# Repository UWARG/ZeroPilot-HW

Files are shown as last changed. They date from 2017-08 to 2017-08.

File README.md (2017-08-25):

# ZeroPilot
WARG's future autopilot to replace the PicPilot

# Installation

After cloning the repo, run `git submodule update --init --recursive` to pull in all the submodules.

If you see rendering issues in the schematic or pcb, check to make sure you've got the most updated submodules. To do this, run: `git submodule update --recursive --remote`

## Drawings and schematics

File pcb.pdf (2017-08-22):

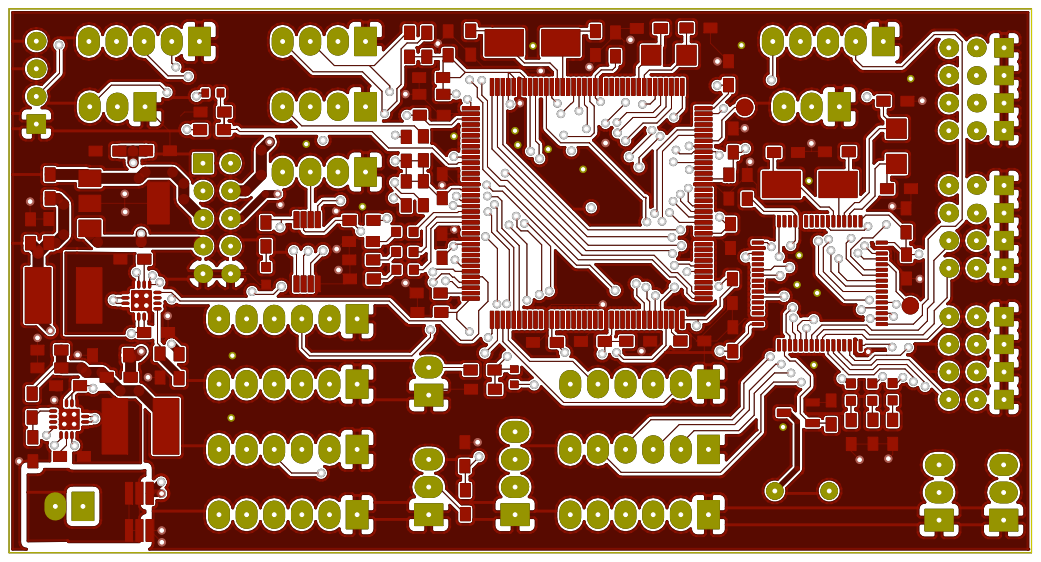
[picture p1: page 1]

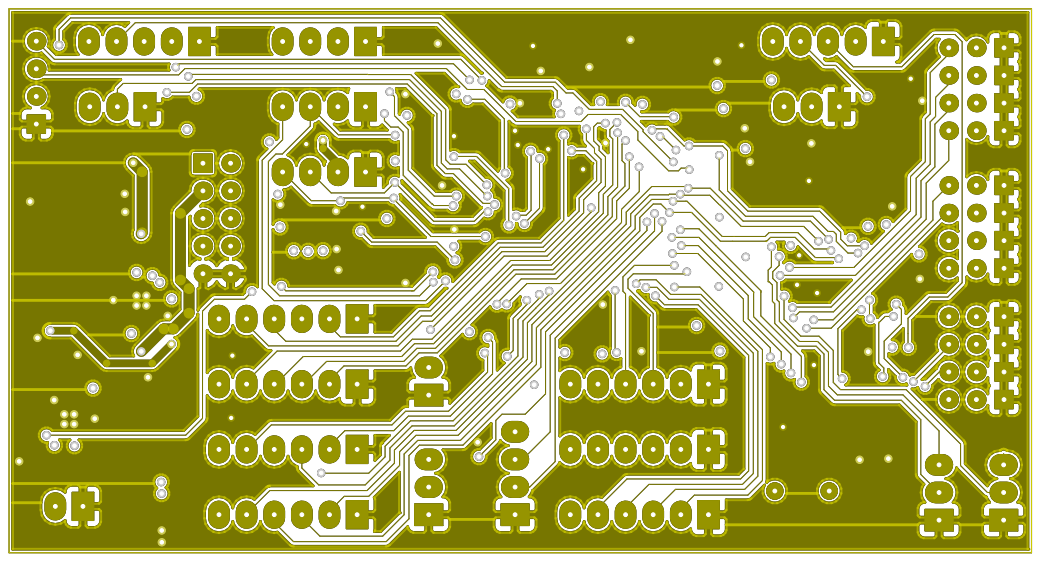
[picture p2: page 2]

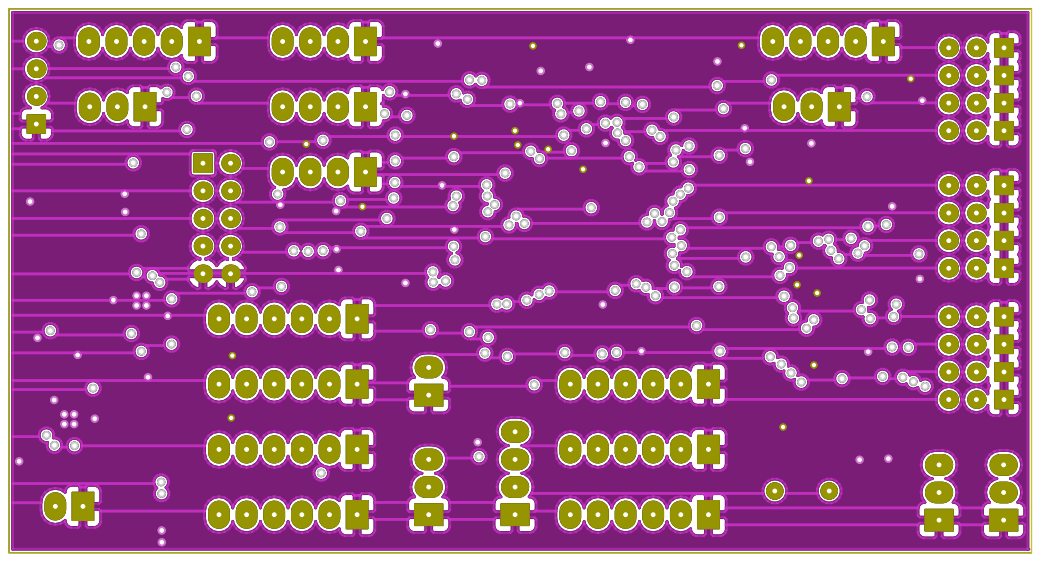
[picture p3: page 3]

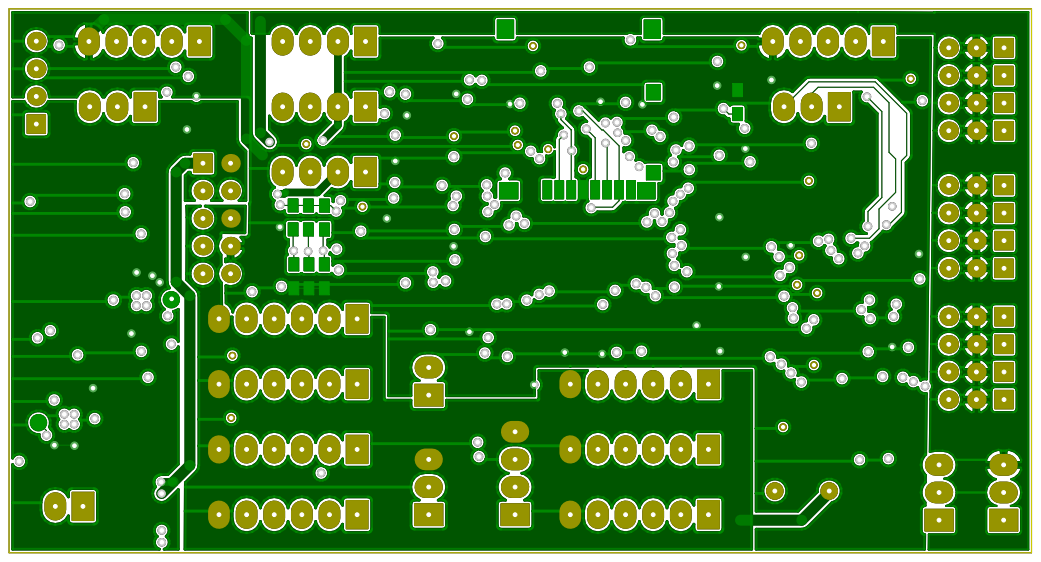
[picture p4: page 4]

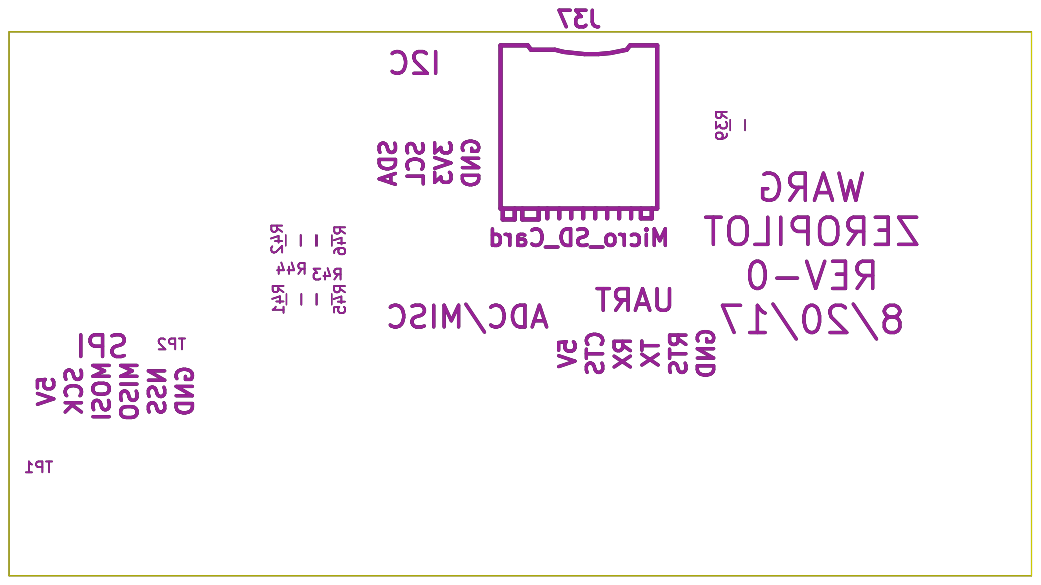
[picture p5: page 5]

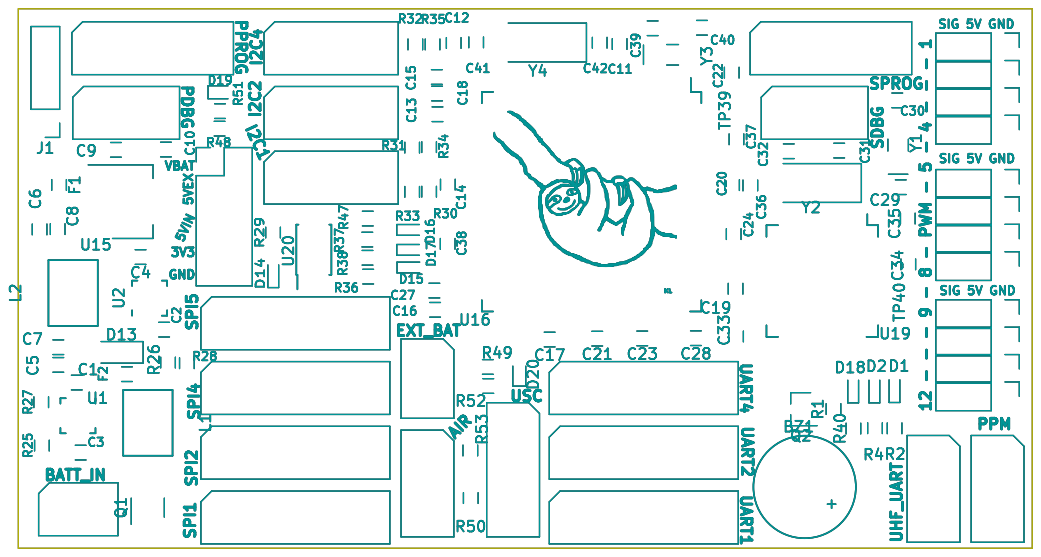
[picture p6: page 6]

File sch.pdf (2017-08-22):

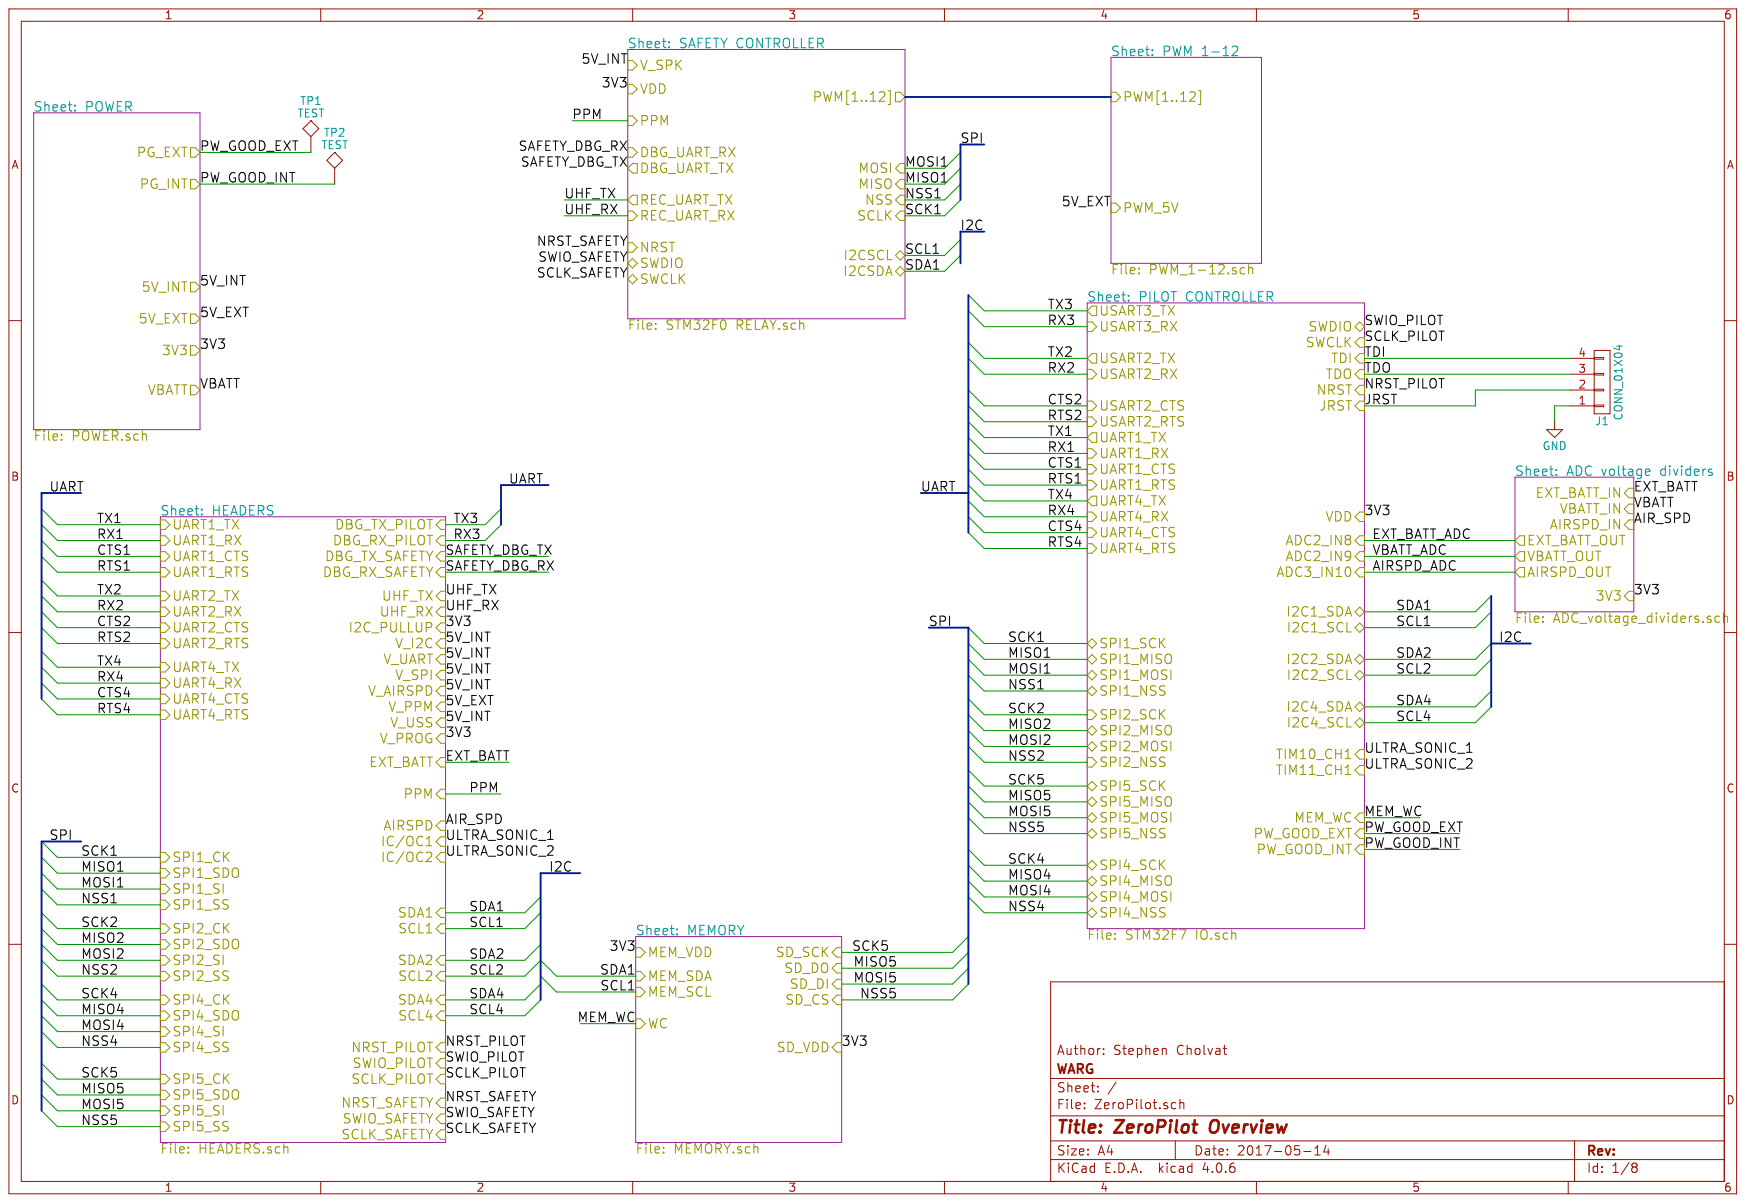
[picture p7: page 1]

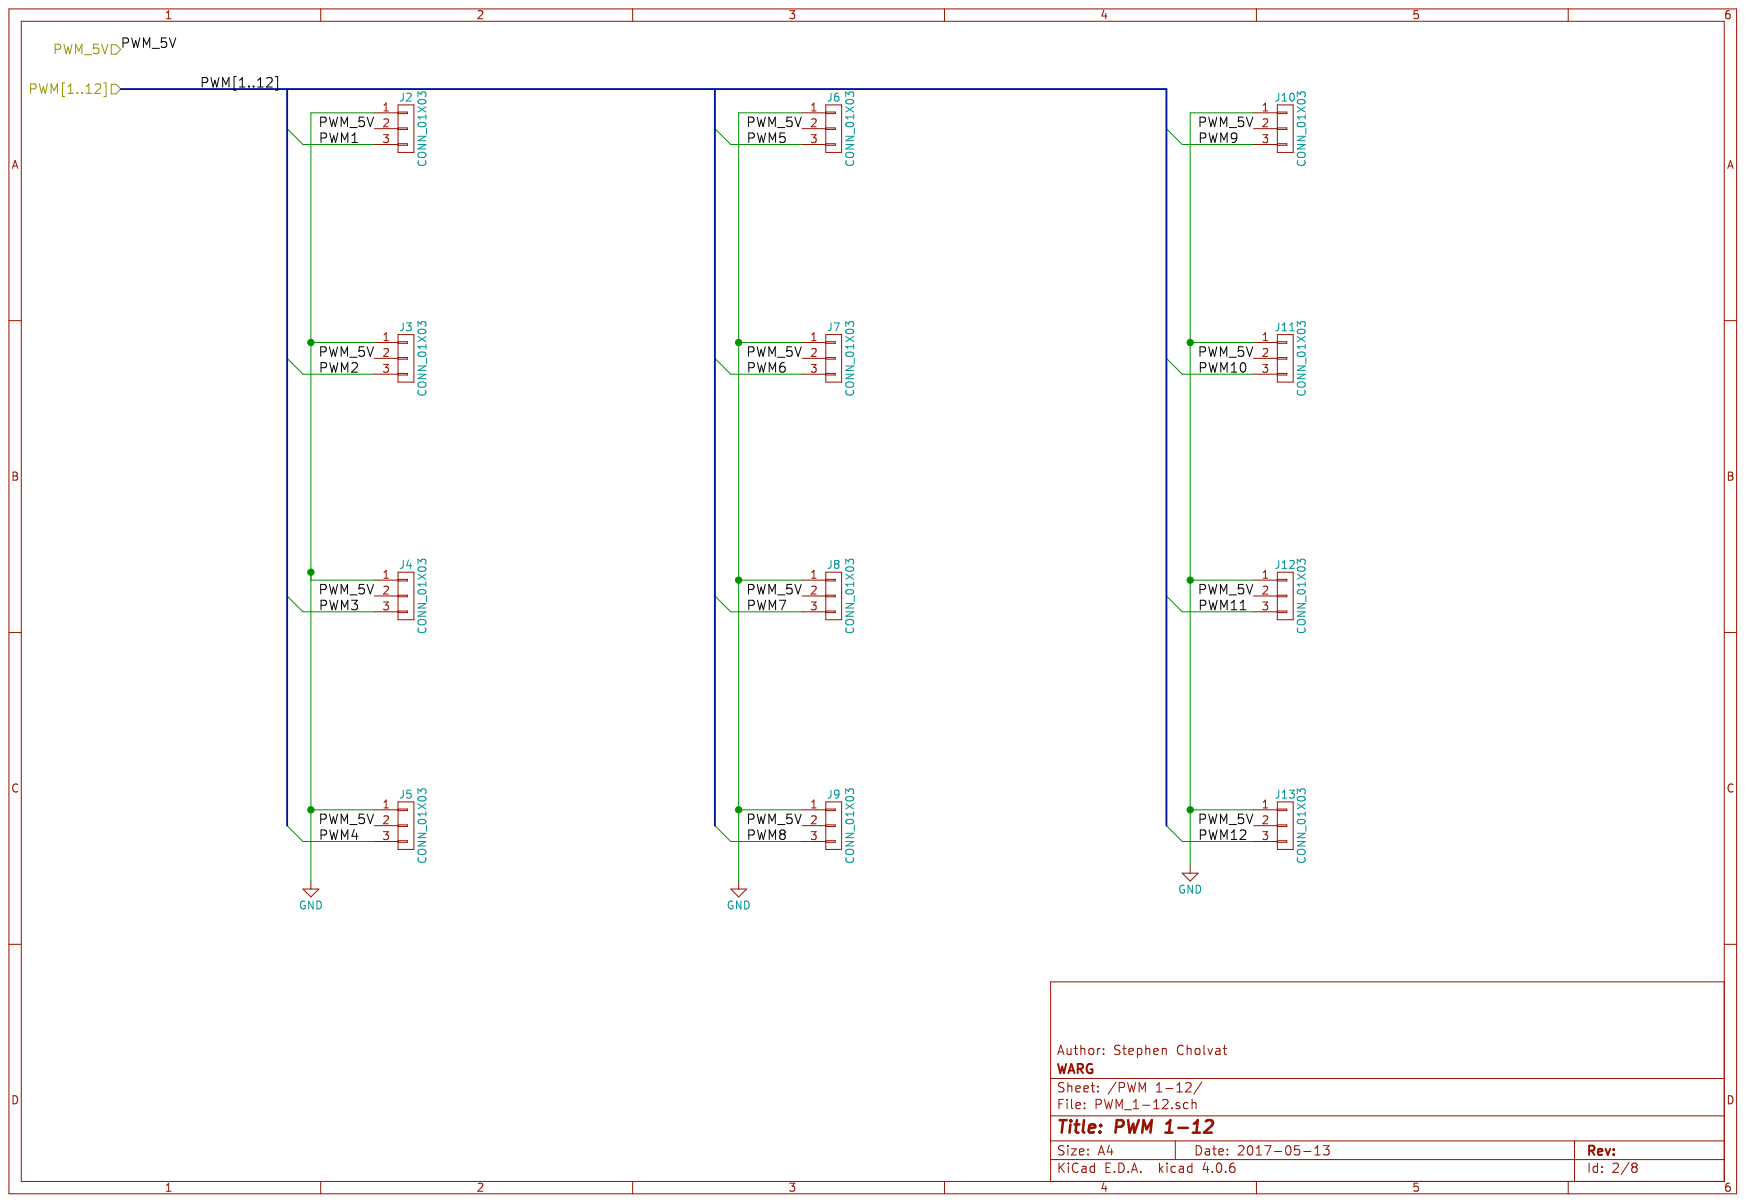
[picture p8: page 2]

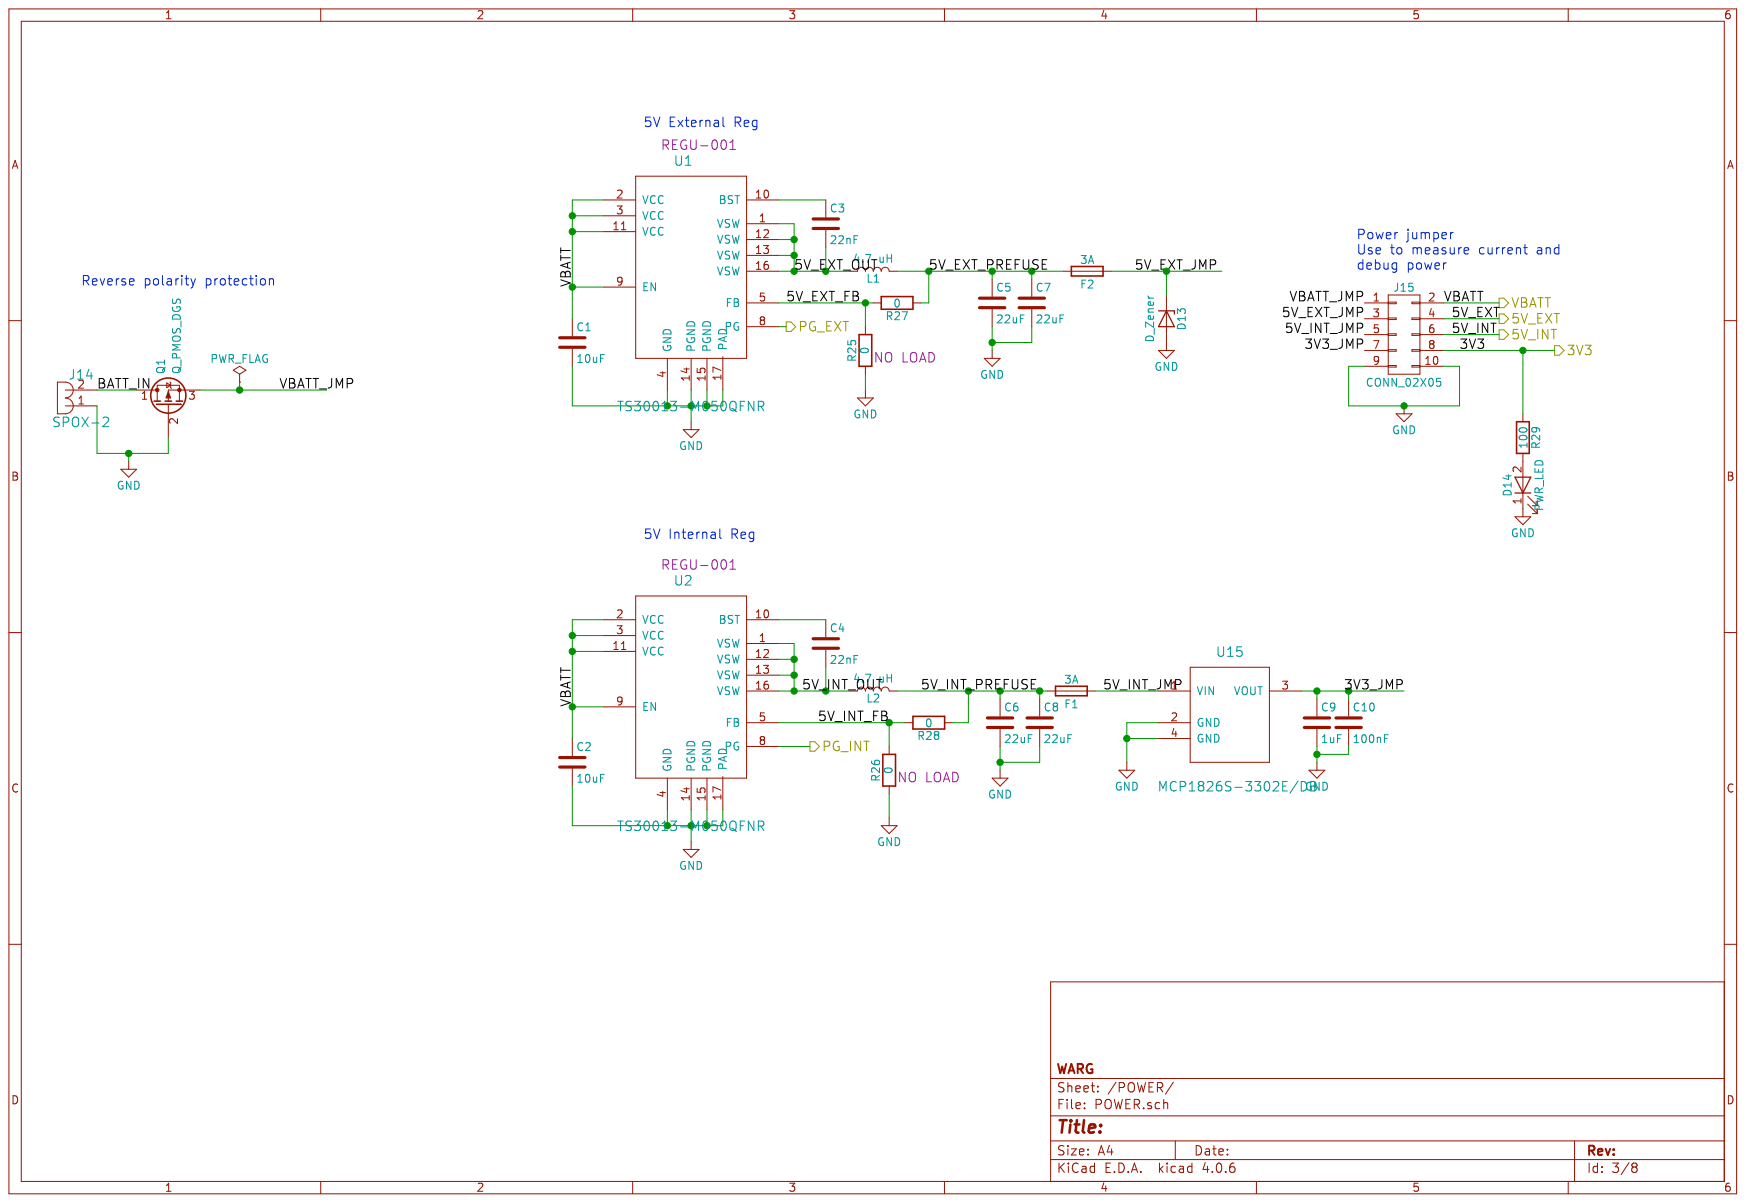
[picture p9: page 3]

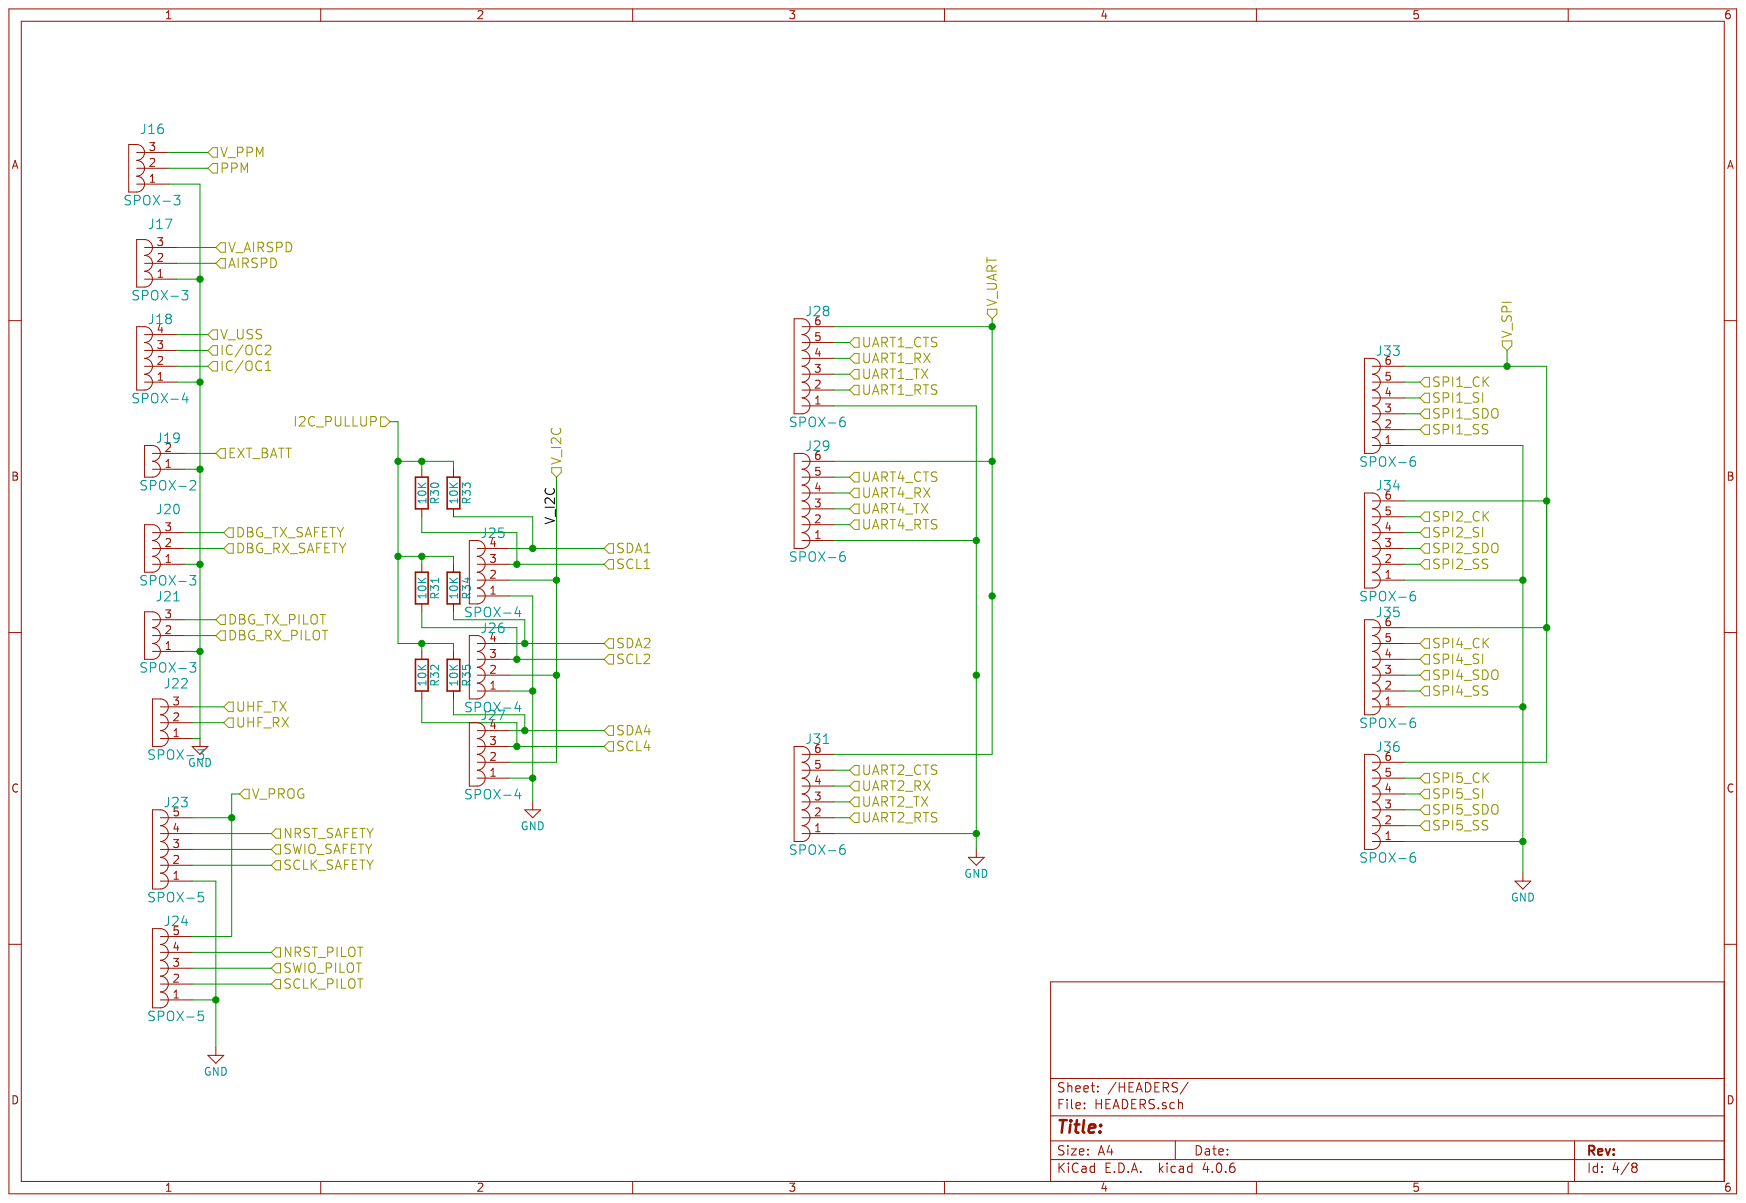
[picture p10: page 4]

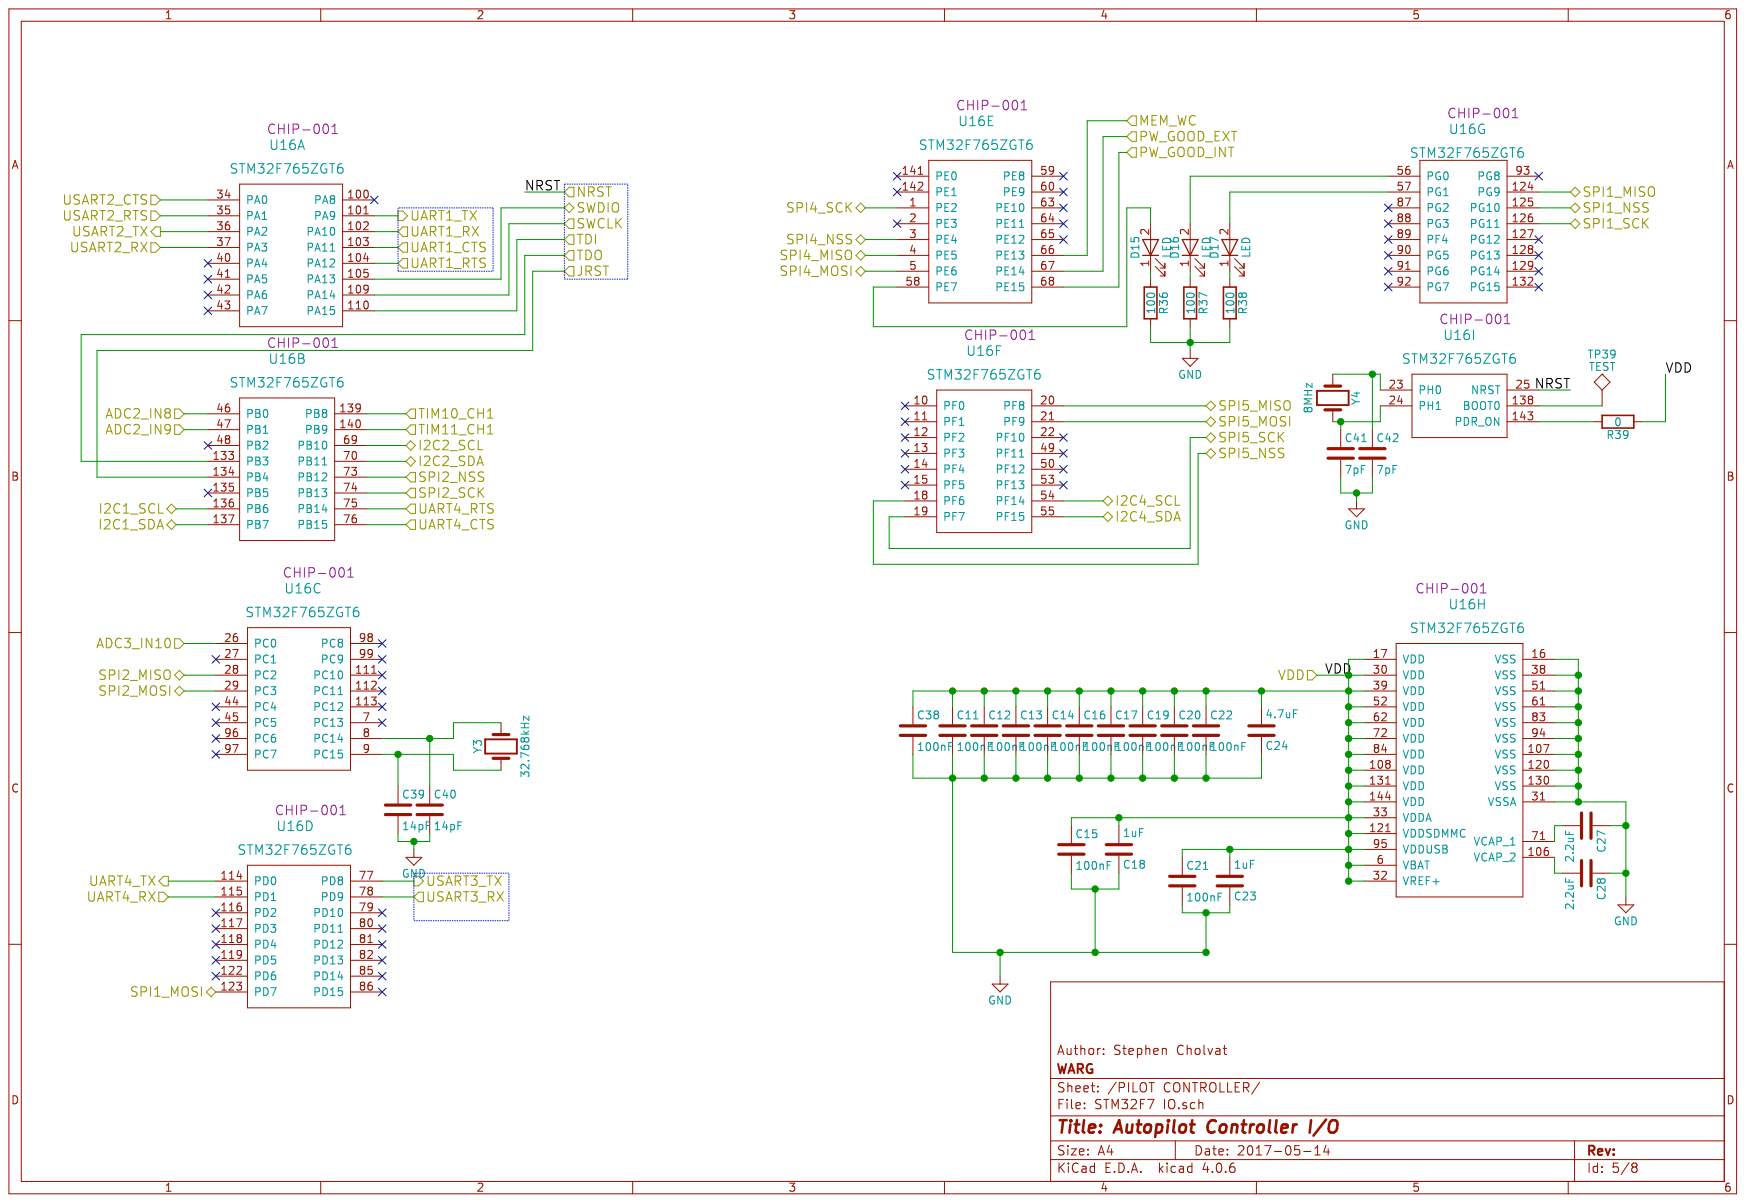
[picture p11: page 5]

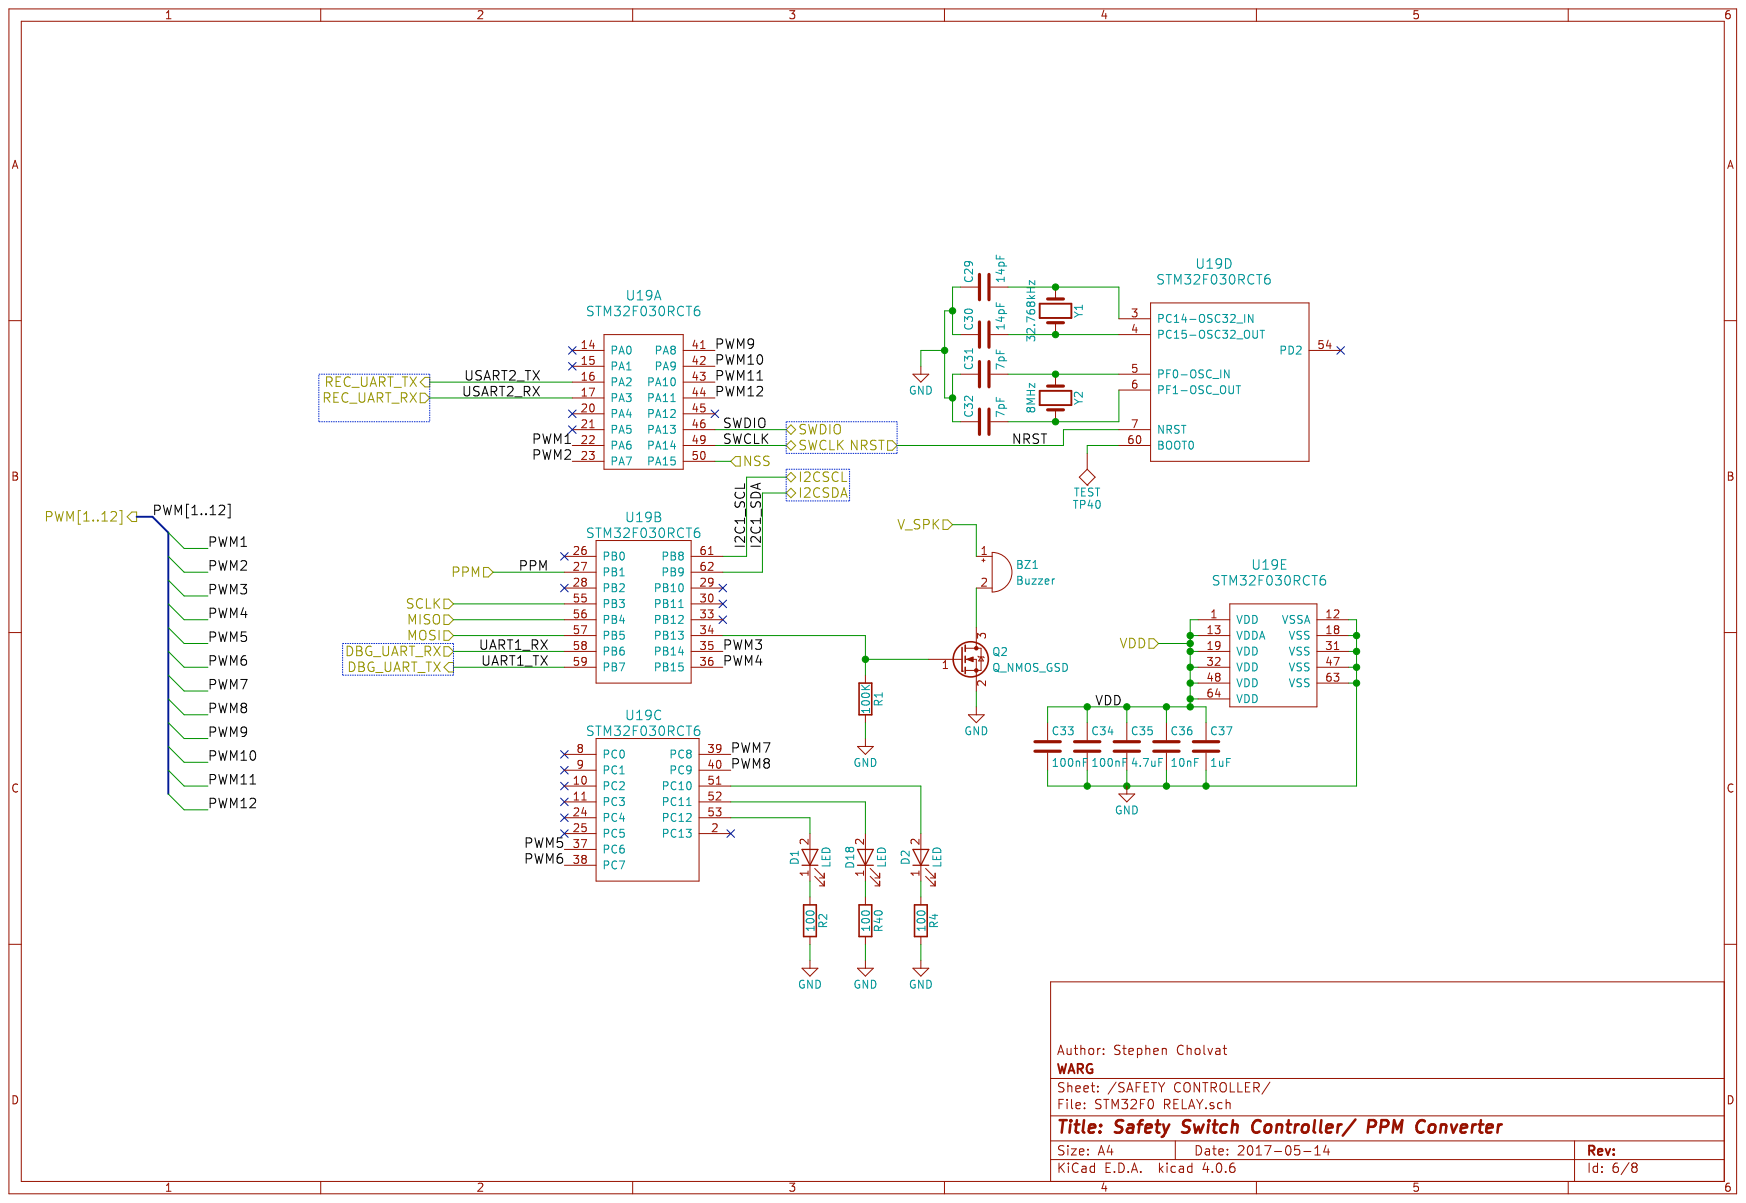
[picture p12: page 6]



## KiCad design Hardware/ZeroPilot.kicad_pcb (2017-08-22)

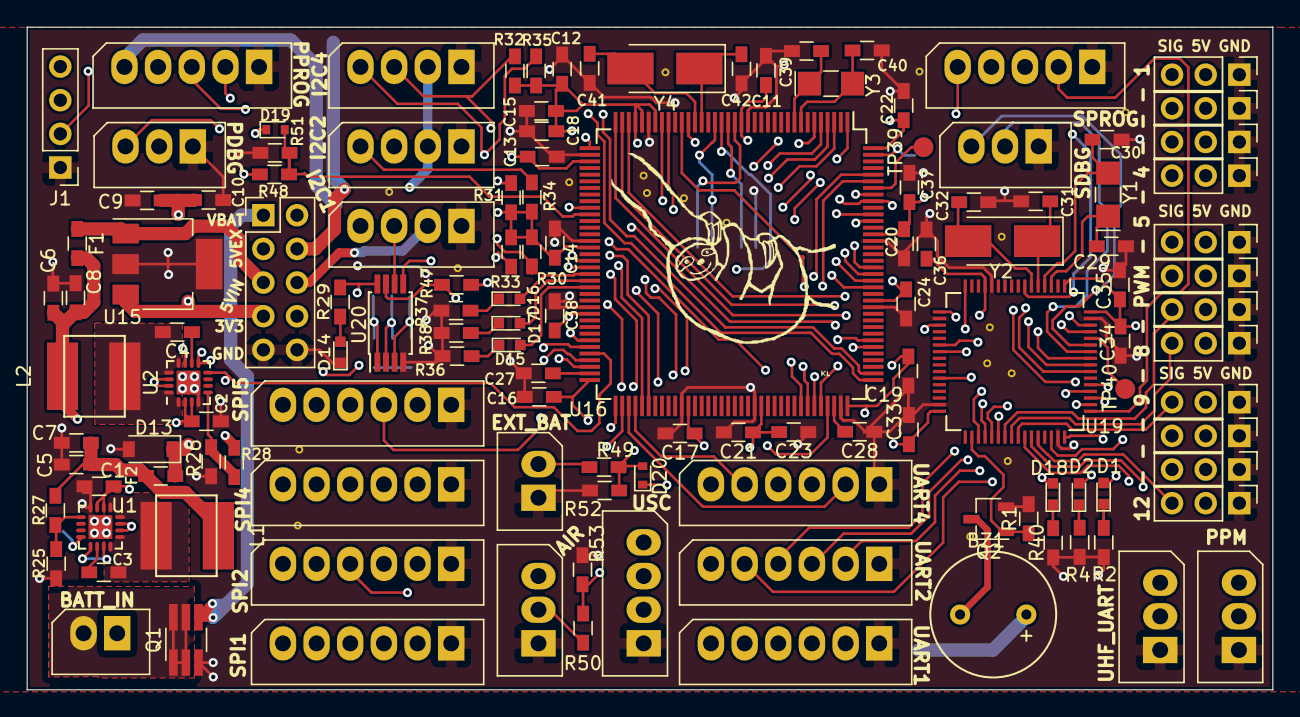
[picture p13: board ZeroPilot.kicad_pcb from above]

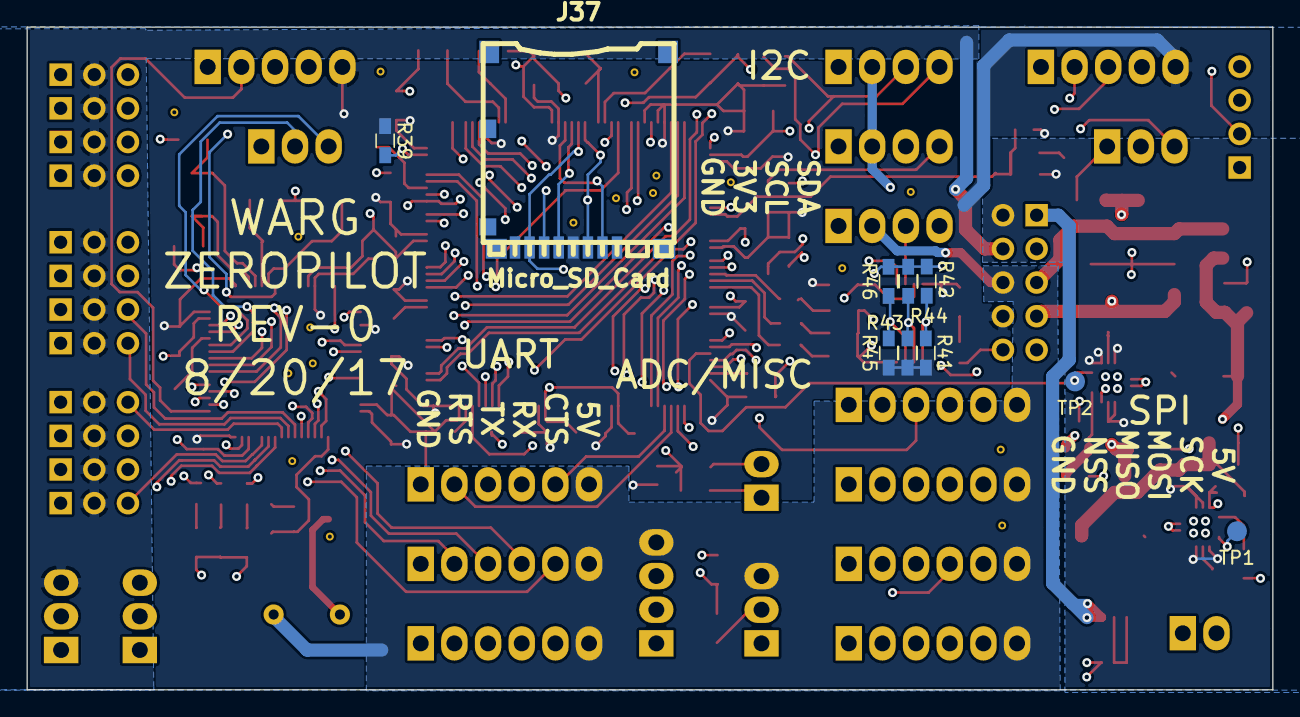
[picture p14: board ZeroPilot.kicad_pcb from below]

Board: 4 copper layers, 94.0 x 50.0 mm, 138 parts (10 on the bottom side), 121 nets.

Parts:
BZ1: Buzzer; AI-1027-TWT-3V-R
C1, C2: 10uF; R_0603_HandSoldering
C3, C4: 22nF; R_0603_HandSoldering
C5, C6, C7, C8: 22uF; R_0603_HandSoldering
C9, C18, C23, C37: 1uF; R_0603_HandSoldering
C10, C11, C12, C13, C14, C15, C16, C17, C19, C20, C21, C22, C33, C34, C38: 100nF; R_0603_HandSoldering
C24, C35: 4.7uF; R_0603_HandSoldering
C27, C28: 2.2uF; R_0603_HandSoldering
C29, C30, C39, C40: 14pF; R_0603_HandSoldering
C31, C32, C41, C42: 7pF; R_0603_HandSoldering
C36: 10nF; R_0603_HandSoldering
D1, D2, D15, D16, D17, D18: LED; LED_0603
D13: D_Zener; D_SOD-123
D14: PWR_LED; LED_0603
D19, D20: D; D_SOD-523
F1, F2: 3A; R_0603_HandSoldering
J1: CONN_01X04; Pin_Header_Straight_1x04_Pitch2.54mm
J2, J3, J4, J5, J6, J7, J8, J9, J10, J11, J12, J13: CONN_01X03; Pin_Header_Straight_1x03_Pitch2.54mm
J14, J19: SPOX-2; Molex_SPOX-5267_22-03-5025_02x2.54mm_Straight
J15: CONN_02X05; Pin_Header_Straight_2x05_Pitch2.54mm
J16, J17, J20, J21, J22: SPOX-3; Molex_SPOX-5267_22-03-5035_03x2.54mm_Straight
J18, J25, J26, J27: SPOX-4; Molex_SPOX-5267_22-03-5045_04x2.54mm_Straight
J23, J24: SPOX-5; Molex_SPOX-5267_22-03-5055_05x2.54mm_Straight
J28, J29, J31, J33, J34, J35, J36: SPOX-6; Molex_SPOX-5267_22-03-5065_06x2.54mm_Straight
J37: Micro_SD_Card; micro_sd
L1, L2: 4.7 uH; 5.1x6.5
Q1: Q_PMOS_DGS; TSOT-23-6_MK06A_HandSoldering
Q2: Q_NMOS_GSD; TSOT-23
R1: 100K; R_0603_HandSoldering
R2, R4, R29, R36, R37, R38, R40: 100; R_0603_HandSoldering
R25, R26, R27, R28, R39, R41, R43, R45: 0; R_0603_HandSoldering
R30, R31, R32, R33, R34, R35, R42, R44, R46, R47: 10K; R_0603_HandSoldering
R48, R49: 150K; R_0603_HandSoldering
R50: 11K; R_0603_HandSoldering
R51, R52, R53: 22K; R_0603_HandSoldering
TP1, TP2, TP39, TP40: TEST; Measurement_Point_Round-SMD-Pad_Small
U1, U2: TS30013-M050QFNR; QFN-16-1EP_3x3mm_Pitch0.5mm
U15: MCP1826S-3302E/DB; SOT-223
U16: STM32F765ZGT6; LQFP-144_20x20mm_Pitch0.5mm
U19: STM32F030RCT6; LQFP-64_10x10mm_Pitch0.5mm
U20: M24C64-WDW6TP; TSSOP-8_4.4x3mm_Pitch0.65mm
Y1, Y3: 32.768kHz; Crystal_SMD_MicroCrystal_CC7V-T1A-2pin_3.2x1.5mm_HandSolder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
Y2, Y4: 8MHz; Crystal_SMD_5032-2pin_5.0x3.2mm_HandSoldering

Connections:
/3V3: C11.1, C12.1, C13.1, C14.1, C15.1, C16.1, C17.1, C18.2, C19.1, C20.1, C21.1, C22.1, C23.2, C24.2, C33.1, C34.1, C35.1, C36.1, C37.1, C38.1, D19.1, D20.1, J15.8, J23.5, J24.5, J37.4, R29.1, R30.1, R31.1, R32.1, R33.1, R34.1, R35.1, R39.1, R41.1, R43.1, R45.1, R47.1, U16.6, U16.17, U16.30, U16.32, U16.33, U16.39, U16.52, U16.62, U16.72, U16.84, U16.95, U16.108, U16.121, U16.131, U16.144, U19.1, U19.13, U19.19, U19.32, U19.48, U19.64, U20.8
/5V_EXT: J2.2, J3.2, J4.2, J5.2, J6.2, J7.2, J8.2, J9.2, J10.2, J11.2, J12.2, J13.2, J15.4, J16.3
/5V_INT: BZ1.1, J15.6, J17.3, J18.4, J25.2, J26.2, J27.2, J28.6, J29.6, J31.6, J33.6, J34.6, J35.6, J36.6
/AIRSPD_ADC: R50.1, R53.1, U16.26
/AIR_SPD: J17.2, R50.2
/CTS1: J28.5, U16.103
/CTS2: J31.5, U16.34
/CTS4: J29.5, U16.76
/EXT_BATT: J19.2, R49.2
/EXT_BATT_ADC: D20.2, R49.1, R52.1, U16.46
/JRST: J1.2, U16.134
/MEMORY/E1: R41.2, R42.1, U20.1
/MEMORY/E2: R43.2, R44.1, U20.2
/MEMORY/E3: R45.2, R46.1, U20.3
/MEM_WC: R47.2, U16.66, U20.7
/MISO1: J33.3, U16.124, U19.56
/MISO2: J34.3, U16.28
/MISO4: J35.3, U16.4
/MISO5: J36.3, J37.7, U16.20
/MOSI1: J33.4, U16.123, U19.57
/MOSI2: J34.4, U16.29
/MOSI4: J35.4, U16.5
/MOSI5: J36.4, J37.3, U16.21
/NRST_PILOT: J24.4, U16.25
/NRST_SAFETY: J23.4, U19.7
/NSS1: J33.2, U16.125, U19.50
/NSS2: J34.2, U16.73
/NSS4: J35.2, U16.3
/NSS5: J36.2, J37.2, U16.18
/POWER/3V3_JMP: C9.1, C10.1, J15.7, U15.3
/POWER/5V_EXT_FB: R25.2, R27.2, U1.5
/POWER/5V_EXT_JMP: D13.1, F2.1, J15.3
/POWER/5V_EXT_OUT: C3.2, L1.1, U1.1, U1.12, U1.13, U1.16
/POWER/5V_EXT_PREFUSE: C5.1, C7.1, F2.2, L1.2, R27.1
/POWER/5V_INT_FB: R26.2, R28.2, U2.5
/POWER/5V_INT_JMP: F1.1, J15.5, U15.1
/POWER/5V_INT_OUT: C4.2, L2.1, U2.1, U2.12, U2.13, U2.16
/POWER/5V_INT_PREFUSE: C6.1, C8.1, F1.2, L2.2, R28.1
/POWER/BATT_IN: J14.2, Q1.1
/POWER/VBATT_JMP: J15.1, Q1.3
/PPM: J16.2, U19.27
/PWM 1-12/PWM1: J2.3, U19.22
/PWM 1-12/PWM2: J3.3, U19.23
/PWM 1-12/PWM3: J4.3, U19.35
/PWM 1-12/PWM4: J5.3, U19.36
/PWM 1-12/PWM5: J6.3, U19.37
/PWM 1-12/PWM6: J7.3, U19.38
/PWM 1-12/PWM7: J8.3, U19.39
/PWM 1-12/PWM8: J9.3, U19.40
/PWM 1-12/PWM9: J10.3, U19.41
/PWM 1-12/PWM10: J11.3, U19.42
/PWM 1-12/PWM11: J12.3, U19.43
/PWM 1-12/PWM12: J13.3, U19.44
/PW_GOOD_EXT: TP1.1, U1.8, U16.67
/PW_GOOD_INT: TP2.1, U2.8, U16.68
/RTS1: J28.2, U16.104
/RTS2: J31.2, U16.35
/RTS4: J29.2, U16.75
/RX1: J28.4, U16.102
/RX2: J31.4, U16.37
/RX3: J21.2, U16.78
/RX4: J29.4, U16.115
/SAFETY_DBG_RX: J20.2, U19.58
/SAFETY_DBG_TX: J20.3, U19.59
/SCK1: J33.5, U16.126, U19.55
/SCK2: J34.5, U16.74
/SCK4: J35.5, U16.1
/SCK5: J36.5, J37.5, U16.19
/SCL1: J25.3, R30.2, U16.136, U19.61, U20.6
/SCL2: J26.3, R31.2, U16.69
/SCL4: J27.3, R32.2, U16.54
/SCLK_PILOT: J24.2, U16.109
/SCLK_SAFETY: J23.2, U19.49
/SDA1: J25.4, R33.2, U16.137, U19.62, U20.5
/SDA2: J26.4, R34.2, U16.70
/SDA4: J27.4, R35.2, U16.55
/SWIO_PILOT: J24.3, U16.105
/SWIO_SAFETY: J23.3, U19.46
/TDI: J1.4, U16.110
/TDO: J1.3, U16.133
/TX1: J28.3, U16.101
/TX2: J31.3, U16.36
/TX3: J21.3, U16.77
/TX4: J29.3, U16.114
/UHF_RX: J22.2, U19.17
/UHF_TX: J22.3, U19.16
/ULTRA_SONIC_1: J18.2, U16.139
/ULTRA_SONIC_2: J18.3, U16.140
/VBATT: C1.1, C2.1, J15.2, R48.2, U1.2, U1.3, U1.9, U1.11, U2.2, U2.3, U2.9, U2.11
/VBATT_ADC: D19.2, R48.1, R51.1, U16.47
GND: C1.2, C2.2, C5.2, C6.2, C7.2, C8.2, C9.2, C10.2, C11.2, C12.2, C13.2, C14.2, C15.2, C16.2, C17.2, C18.1, C19.2, C20.2, C21.2, C22.2, C23.1, C24.1, C27.1, C28.1, C29.1, C30.1, C31.1, C32.1, C33.2, C34.2, C35.2, C36.2, C37.2, C38.2, C39.2, C40.2, C41.2, C42.2, D13.2, D14.1, J1.1, J2.1, J3.1, J4.1, J5.1, J6.1, J7.1, J8.1, J9.1, J10.1, J11.1, J12.1, J13.1, J14.1, J15.9, J15.10, J16.1, J17.1, J18.1, J19.1, J20.1, J21.1, J22.1, J23.1, J24.1, J25.1, J26.1, J27.1, J28.1, J29.1, J31.1, J33.1, J34.1, J35.1, J36.1, J37.6, Q1.2, Q2.2, R1.2, R2.2, R4.2, R25.1, R26.1, R36.2, R37.2, R38.2, R40.2, R42.2, R44.2, R46.2, R51.2, R52.2, R53.2, U1.4, U1.14, U1.15, U1.17, U2.4, U2.14, U2.15, U2.17, U15.2, U15.4, U16.16, U16.31, U16.38, U16.51, U16.61, U16.83, U16.94, U16.107, U16.120, U16.130, U19.12, U19.18, U19.31, U19.47, U19.63, U20.4
unnamed: BZ1.2, Q2.3
unnamed: C3.1, U1.10
unnamed: C4.1, U2.10
unnamed: C27.2, U16.71
unnamed: C28.2, U16.106
unnamed: C29.2, U19.3, Y1.1
unnamed: C30.2, U19.4, Y1.2
unnamed: C31.2, U19.5, Y2.1
unnamed: C32.2, U19.6, Y2.2
unnamed: C39.1, U16.9, Y3.1
unnamed: C40.1, U16.8, Y3.2
unnamed: C41.1, U16.24, Y4.2
unnamed: C42.1, U16.23, Y4.1
unnamed: D1.1, R2.1
unnamed: D1.2, U19.53
unnamed: D2.1, R4.1
unnamed: D2.2, U19.51
unnamed: D14.2, R29.2
unnamed: D15.1, R36.1
unnamed: D15.2, U16.58
unnamed: D16.1, R37.1
unnamed: D16.2, U16.56
unnamed: D17.1, R38.1
unnamed: D17.2, U16.57
unnamed: D18.1, R40.1
unnamed: D18.2, U19.52
unnamed: Q2.1, R1.1, U19.34
unnamed: R39.2, U16.143
unnamed: TP39.1, U16.138
unnamed: TP40.1, U19.60

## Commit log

2017-05-13 Initial commit setting up the project
    [WARGPilot.kicad_pcb, WARGPilot.sch]
2017-05-14 Added PWM switch stuff
    [PWM.sch, PWM_1-12.sch, WARGPilot.sch]
2017-05-14 Renamed project
    [PWM.sch, PWM_1-12.sch, PilotZero.sch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]
2017-05-14 Added gitignore, started adding STM
    [WARGPilot.sch]
2017-05-14 ALL THE POWER
    [POWER.sch, PWM.sch, PWM_1-12.sch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]
2017-05-14 Added F7 chip
    [POWER.sch, PWM.sch, PWM_1-12.sch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]
2017-05-14 Added F0 chip
    [POWER.sch, PWM.sch, PWM_1-12.sch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]
2017-05-14 Added relay chip
    [_saved_STM32F0 RELAY.sch]
2017-05-14 Connected Relay together
    [STM32F0 RELAY.sch, ZeroPilot.sch, _saved_STM32F0 RELAY.sch]
2017-05-16 Added F7 Circuitry
    Added way too much for 1 commit.
    [POWER.sch, PWM.sch, PWM_1-12.sch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]
2017-05-16 Added extra IOs
    [STM32F7 IO.sch, ZeroPilot.sch]
2017-05-17 Added headers
    [HEADERS.sch, POWER.sch, PWM.sch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]
2017-05-18 Reconfiguring pinout round 2
    [STM32F7 IO.sch, ZeroPilot.sch]
2017-05-18 first rough draft without headers
    [BUFFER.sch, HEADERS.sch, POWER.sch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]
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2017-05-18 branch to make PR for review
    I should have made a separate branch for the development and then merged
    it, but its too late now.
    [BUFFER.sch, HEADERS.sch, POWER.sch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]
2017-05-19 Added a lot of debug
    [POWER.sch, PWM.sch, STM32F7 IO.sch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]
2017-05-20 Added memory
    [BUFFER.sch, HEADERS.sch, POWER.sch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]
2017-05-22 Fixed some BOM stuff
    fixed BOM for non RLC components
    [BUFFER.sch, HEADERS.sch, MEMORY.sch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]
2017-05-23 Finished RLC bom stuff
    [BUFFER.sch, HEADERS.sch, MEMORY.sch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]
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2017-05-25 PCB?!
    Added initial PCB file with ratsnest. footprint library still needs to
    be setup.
    [BUFFER.sch, HEADERS.sch, MEMORY.sch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]
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2017-05-28 Fixed serge suggestions
    [ADC_voltage_dividers.sch, BUFFER.sch, HEADERS.sch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]
2017-05-29 commit before my computer restarts
    [ADC_voltage_dividers.sch, BUFFER.sch, HEADERS.sch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]
2017-05-29 vague pcb placements
    still needs the sd card footprint
    [ZeroPilot.kicad_pcb, _saved_ZeroPilot.sch]
2017-05-29 routed PWM and SEL bus
    [PWM.sch, STM32F0 RELAY.sch, STM32F7 IO.sch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]
2017-05-29 finished safety controller routing
    [PWM.sch, ZeroPilot.kicad_pcb, _saved_STM32F0 RELAY.sch]
2017-05-30 rough power circuit routing
    roughly put together the routing for power circuit, but it needs to be
    replaced with thicker traces or copper pours
    [ADC_voltage_dividers.sch, MEMORY.sch, STM32F0 RELAY.sch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]
2017-05-31 placed headers in roughly correct spot
    [BUFFER.sch, STM32F7 IO.sch, ZeroPilot.kicad_pcb]
2017-06-01 adc routing, made board smaller
    [STM32F0 RELAY.sch, STM32F7 IO.sch, ZeroPilot.kicad_pcb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]
2017-06-01 imported micro sd footprint
    [ADC_voltage_dividers.sch, BUFFER.sch, MEMORY.sch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]
2017-06-02 realizing how hard routing headers is
    [ZeroPilot.kicad_pcb]
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2017-06-04 finished all routing except gnd
    [ZeroPilot.kicad_pcb]
2017-06-04 A fully routed (shitty) board!
    [ZeroPilot.kicad_pcb]
2017-06-05 Fixed random connection errors
    [ZeroPilot.kicad_pcb]
2017-06-06 This power is HUGE
    Made some big traces and pours for power. Need to do some ground layer
    stiching to fix the ground plane still
    [POWER.sch, ZeroPilot.kicad_pcb]
2017-06-06 Holy Power
    Added a ton of stitching to the power section. Never enough vias.
    [ZeroPilot.kicad_pcb]
2017-06-06 Holy Pilot
    Added stiching around STMF7 chip
    [ZeroPilot.kicad_pcb]
2017-06-07 Is too much stitching a thing?
    Its concerning when you start to become worried about the structural
    integrity of the board because of too many vias... oh well, I think its
    fine
    [ZeroPilot.kicad_pcb]
2017-06-08 Updated sd card footprint with shield pin
    [MEMORY.sch, ZeroPilot.kicad_pcb]
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2017-07-30 Restarted work
    Removed OC and SEL busses. Still need to add clocks.
    [ADC_voltage_dividers.sch, HEADERS.sch, MEMORY.sch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]
2017-08-12 Added clock, cleaned up files
    [BUFFER.sch, PWM.sch, STM32F0 RELAY.sch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]
2017-08-12 Placement and preminiary routing
    [ADC_voltage_dividers.sch, HEADERS.sch, MEMORY.sch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]
2017-08-12 power placement and experimental routing
    [ADC_voltage_dividers.sch, HEADERS.sch, MEMORY.sch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]
2017-08-12 Placed oscillators
    [ZeroPilot.kicad_pcb, _saved_POWER.sch, _saved_STM32F7 IO.sch]
2017-08-12 Routed decoupling caps and power supply
    [POWER.sch, STM32F7 IO.sch, ZeroPilot.kicad_pcb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]
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2017-08-12 Fully placed board
    Placed board, also fixed I2C pullup bug
    [ZeroPilot.kicad_pcb, ZeroPilot.sch]
2017-08-12 Spaced out conns to 6mm
    Spaced out connectors to 6mm to please serge (and anyone else who tries to plug things in)
    [ZeroPilot.kicad_pcb]
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2017-08-13 routed UART, started SPI
    [ZeroPilot.kicad_pcb]
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2017-08-13 Updated schematic to make routing easier
    [HEADERS.sch, STM32F7 IO.sch, ZeroPilot.sch]
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2017-08-15 Copper balancing
    Copper balanced the inner layers
    [ZeroPilot.kicad_pcb]
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2017-08-20 Bottom silk screen and improved stiching
    [ADC_voltage_dividers.sch, HEADERS.sch, MEMORY.sch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]
2017-08-20 Fixed DRC error
    [ZeroPilot.kicad_pcb]
2017-08-22 Tried fixing somethings
    Not complete yet but made the changes Ian mentioned
    [ADC_voltage_dividers.sch, HEADERS.sch, POWER.sch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]
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2017-08-25 Removed KiCad BOM Wizard
    I added a BOM script to WARG-KiCad repo so this is no longer needed
2018-03-28 Re-routed 3V3 input to after jumper
    [ADC_voltage_dividers.sch, HEADERS.sch, MEMORY.sch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]
2018-03-28 Added BOOT0 pulldown, fixed Safety DBG lines
    [STM32F0 RELAY.sch, STM32F7 IO.sch]
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2018-03-28 Fix PPM and Airspeed connector pinouts
    [HEADERS.sch, ZeroPilot.kicad_pcb]
2018-03-28 I'll be honest i don't know what this is
    [HEADERS.sch]
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2018-06-05 Replaced Semtec buck with TI one for 5V internal/external. External now outputs 6V to accomodate servos. Added USB option
    [POWER.sch]
2018-06-05 Revert "Fixing merge conflicts - local branch was not up-to-date"
    This reverts commit 85b419e2a89eccdb56e88abd646d1b78d4b8e085, reversing
    changes made to 0d71bb5c9bf7651516b12d178fbe9b04fea9e8f8.
    Quote un-quote fixing merge conflicts ended up deleting power page...
    [ADC_voltage_dividers.sch, HEADERS.sch, MEMORY.sch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]
2018-06-07 Sensors sheet with IMU and altimeter (#9)
    * Add files via upload
    * Added IMU and Altimeter schematics and footprints
    * Added new SENSORS sheet with the IMU and Altimeter
    * Fixed altimeter schematic
    * Removed duplicate folder
    * Removed pull up resistors from altimeter
    * Added part nums to IMU and altimeter, updated csv file
    * Added footprint values and part nums to capacitors
    Also added part nums on the sheet to the sensors, however they already exist in the footprint editor
    * Added test points, updated footprint values, fixed J1, replaced connectors
    * Updated fp-lib-table
    * Updated footprint field for capacitors in sensors sheet
    * Fixed part_num field in P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
    [ADC_voltage_dividers.sch, HEADERS.sch, MEMORY.sch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]
2018-06-07 Added USB Interface Sheet
    Added hierarchically, under ZeroPilot.sch.
    [ADC_voltage_dividers.sch, HEADERS.sch, MEMORY.sch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]
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2018-06-08 Almost Done USB Interface
    [USB INTERFACE.sch]
2018-06-17 Finalized USB Interface
    Added SWD line resistors
    [USB INTERFACE.sch]
2018-06-17 Added USB Interface to ZeroPilot
    Added the USB interface to the rest of the schematic.
    [HEADERS.sch, ZeroPilot.sch]
2018-06-18 Fixed Missing Bits
    Fixed missing crystal part_num and added hierarchical pin for VBUS.
    [USB INTERFACE.sch]
2018-06-19 Added load switch circuit - defaults to batery power when available
    [ADC_voltage_dividers.sch, HEADERS.sch, MEMORY.sch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]
2018-06-19 Bug Fixes
    Fixed some missing connections related to the USB Interface.
    [USB INTERFACE.sch, ZeroPilot.sch]
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2018-06-21 Adjusted for Mergability
    Grabbed latest ZeroPilot.sch and re-added USB Interface sheet to it.
    [ADC_voltage_dividers.sch, HEADERS.sch, MEMORY.sch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]
2018-06-22 Added Test Points for USB Interface
    Added JTAG and UART test points for the FT4232H
    [HEADERS.sch, USB INTERFACE.sch, ZeroPilot.sch]
2018-06-22 Bug Fixes
    Fixed hierarchical pin naming typos
    [USB INTERFACE.sch]
2018-06-23 Fixed Typos
    Fixed typos on the component fields of the Micro USB connector in the USB interface.
    [USB INTERFACE.sch]
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2018-06-23 fixed sensor sheet from merge
    [sensors.sch]
2018-06-24 Added jumpers and ramp-up option on load switches.
    [ADC_voltage_dividers.sch, HEADERS.sch, MEMORY.sch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]
2018-06-24 Scholvat patch 1 (#12)
    * Fixed Sensors.sch sheeet
    Windows hates the world and decides files don't need to be case sensitive, but git does.
    * Delete sensors.sch
    [SENSORS.sch, sensors.sch]
2018-06-26 Removed redundant inverter, added larger diode to solder
    [ADC_voltage_dividers.sch, HEADERS.sch, MEMORY.sch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]
2018-06-26 Fixed HEADERS.sch file
    [HEADERS.sch]
2018-06-26 Fixed merge issues
    [ADC_voltage_dividers.sch, HEADERS.sch, MEMORY.sch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]
2018-07-10 USB Interface REV1 (#13)
    * Connected NRST pins to USB Interface
    Connected the MCUs NRST pins to the GPIO0 pins on the A and B channels of the FT4232H. Also deleted the redundant test points resulting from this.
    * Updated Resistors
    Changed 1K resistors on DBUS1 lines to 220R resistors and 100R resistors on DBUS2 lines to 0R resistors, on the FT4232H.
    * Deleted Old TPs
    * Fixed Bugs
    Noticed my part numbers in the library had been overwritten, so updated to reflect adding them back with new numbers. Also fixed typo with TVS diodes.
    * Fixed one more bug
    Fixed overwritten part num
    [HEADERS.sch, USB INTERFACE.sch, ZeroPilot.sch]
